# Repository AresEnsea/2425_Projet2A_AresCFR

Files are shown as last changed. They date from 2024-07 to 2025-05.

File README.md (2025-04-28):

# 2425_AresCFR
Ce repository contient le travail de l'association Arès dans le cadre de la Coupe de France de Robotique 2024-2025. Il contient tous les fichiers CAO, Kicad, Python, C ainsi que les photos, diagrammes et schémas qui ont fait avancer le projet.

## Répartition
Dépôt du projet de coupe de France de robotique 2024/2025
- 1A : Ce repository contient le travail des 1ères années membres de l'association Arès à l'ENSEA sur les PAMIs de la Coupe de France de Robotique

Read me 1A :
      https://github.com/AresEnsea/2425_Projet2A_AresCFR/blob/main/1A/README.md
      
- 2A : Ce repository contient le travail des 2èmes années membres de l'association Arès à l'ENSEA sur le robot principal de la Coupe de France de Robotique

Read me 2A :
      https://github.com/AresEnsea/2425_Projet2A_AresCFR/blob/main/2A/README.md

WhatsApp Image 2025-04-28 at 09 13 59
WhatsApp Image 2025-04-28 at 09 14 00

https://github.com/user-attachments/assets/8da76ca9-4337-4687-90c1-276035e22721

PAMI_img1

## Règlement
Le but de la compétition est de faire réaliser des actions de différentes difficultés grâce à des robots complétement autonomes, en lien avec le thème de l'année. Cette année le robot principal devra pouvoir se déplacer, déplacer des cannettes et des planches en bois de sorte à les empiler selon l'ordre suivant (2 canettes - 1 planche, 2 canettes - 1 planche , 2 canettes - 1 planche) pour un maximum de 3 étages, chaque étage rapporte plus de points que le précédent, le tout pour atteindre le score le plus grand. Cette année les PAMIs (Petits Actionneur Motorisés Indépendants) censés aider le robot principal en rapportant également des points sont d'une grande importance puisque rapporte en théorie autant de points qiue le robot principal, ils réaliseront des actions simples (déplacement et activation d'un actionneurs), un se distingue parmi eux le "Superstar" qui devra grimper sur l'estrade de la table et se rapprocher le plus du bord sans tomber pour gagner des points.




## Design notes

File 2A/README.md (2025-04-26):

# CDF-2025
Github de la Coupe de France de Robotique!

#REGLEMENTS
https://www.coupederobotique.fr/accueil/le-concours/reglement-2025/
https://www.coupederobotique.fr/wp-content/uploads/Eurobot2025_Rules.pdf

#DIAPO 
[https://enseafr-my.sharepoint.com/:p:/g/personal/antoine_lemarignier_ensea_fr/Eb2eWKZeK-NNrEKdino8REcB281sSVFofJ1WQgk0IBzqbg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](https://enseafr-my.sharepoint.com/:p:/g/personal/antoine_lemarignier_ensea_fr/ESafam9fs7ZCg727WFCmVboB-b12O3MPg7kT_spCKCZYLA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)

## Photo Robot :


## Liste des participants :
- Lorenzo ROMEO
- Antoine LEMARIGNER
- Mateo GOMES
- Nathan BAINARD
- Ewan ZAHRA-THENAULT
- Khalid ZOUHAIR
- Abderhamane EL FELSOUFI 
- Mohamed EL KOURMISS 
- Sammy GROS
- Matis GARBEZ
- Kenny SAINT FLEUR

## Partenaires :
- [x] Wurth
- [x] Elsys Design
- [x] RS
- [x] Acksys

# Etat du Projet 

## PCB MOTHERBOARD : 
- lien : https://github.com/AresEnsea/2425_Projet2A_AresCFR/edit/main/2A/Hardware/Hardware_%C3%A9lectronique/MainBoard/PCB_test/
- [x] Actuellement en V2
## PCBs auxiliaires :
- [x] steppers https://github.com/AresEnsea/2425_Projet2A_AresCFR/tree/main/2A/Hardware/Hardware_%C3%A9lectronique/Auxiliairy_board/PCB_Stepper
- [x] Moteurs base roulante https://github.com/AresEnsea/2425_Projet2A_AresCFR/new/main/2A/Hardware/Hardware_%C3%A9lectronique/Auxiliairy_board/PCB_Moteur
- [x] Servo moteurs https://github.com/AresEnsea/2425_Projet2A_AresCFR/tree/main/2A/Hardware/Hardware_%C3%A9lectronique/Auxiliairy_board/PCB_Servo

## Méca :
lien modèle 3D : https://cad.onshape.com/documents/e7dd6126290aaac8861c9b96/w/d5c385b6723083ea50ea9e11/e/9022f36f38f961f67dfb7efc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
- [x] Base roulante du robot complète
- [x] Pinces attrape canettes
- [x] Chariots élévateurs
- [x] Banderole
- [x] Fixations PCB
- [ ] Management de cables
- [ ] Odométrie
- [ ] Bouton d'arret d'urgence
- [ ] Tirette de démarrage

## ROS2 embarqué
- lien workspace ros : https://github.com/AresEnsea/2425_Projet2A_AresCFR/tree/main/2A/Firmware/ros2_ws
- [x] Liaison UART pi-STM32
- [x] Rosbags moteurs-actionneurs-Lidar
- [x] Interface écran
- [ ] Odométrie
- lien workspace lidar : https://github.com/AresEnsea/2425_Projet2A_AresCFR/tree/main/2A/Firmware/ydlidar_ros2_ws
- [x] Scan fonctionnel
- [ ] Tout mettre dans le workspace principal

## STM32
lien projet STM32 : https://github.com/AresEnsea/2425_Projet2A_AresCFR/tree/main/2A/Firmware/STM32_moteurs
- [x] V1 code stm32 moteurs réagissant à la pi
- [ ] V2 sur le microprocesseur du PCB

## Vision
lien projet Vision : https://github.com/AresEnsea/2425_Projet2A_AresCFR/tree/main/2A/Vision
- [x] Calibration caméra
- [x] Détection Aruco de la table
- [x] Suivi du mouvement d'un Aruco
- [ ] Transformer les informations de la caméra en carte pour le ROS

## Réseau
- [x] Administration de routeurs
- [x] Ping à travers 2 routeurs
- [x] Avoir un réseau transportable à la Coupe
- [ ] Connecter la pi et la jetson à un même réseau wifi pour communiquer
   
# Répartition par tâche :

## 1-ROS2/STM32 :
- Antoine
- Mateo
- Sammy

Le compte rendu de notre équipe sur le software embarqué se trouve dans le ReadMe.md du dossier Firmware :
https://github.com/AresEnsea/2425_Projet2A_AresCFR/blob/main/2A/Firmware/README.md

## 2-Traitement Image :
- Khalid
- Mohamed
- Abderahmane

Le compte rendu de notre équipe sur le traitement d'image est présent ici :
https://github.com/AresEnsea/2425_Projet2A_AresCFR/blob/main/2A/Vision/README.md

## 3-PCB :
- Kenny
- Ewan

Le compte rendu de notre équipe sur le PCB est présent ici :
https://github.com/AresEnsea/2425_Projet2A_AresCFR/tree/main/2A/Hardware/Hardware_électronique/readme.md

## 4-Mécanique :
- Lorenzo
- Matis
  
Le compte rendu pour la partie mécanique est disponible ici :
https://github.com/AresEnsea/2425_Projet2A_AresCFR/tree/main/2A/Hardware/Hardware_Mécanique/README.md

## 5-Réseau :
- Nathan
  
Le compte rendu pour la partie réseau est disponible ici :
https://github.com/AresEnsea/2425_Projet2A_AresCFR/tree/main/2A/Reseau/README.md

## 6-Planification :
- Mateo
- Antoine

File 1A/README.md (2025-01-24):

# Projet PAMI - Coupe de France des 1A

Ce projet consiste en la conception et la construction des robots **PAMI** pour la Coupe de France de Robotique.

## Description du robot actuel

Le robot actuel est équipé des éléments suivants :  
- Un **module suiveur de ligne** avec **4 capteurs/récepteurs infrarouges**.  
- Un **servomoteur** utilisé pour l'algorithme d'évitement d'obstacles.  
- Un **module ultrason** pour l'estimation des distances et la détection d'obstacles.  
- Une carte **Nucleo** pour la commande et la gestion des données.  
- Un **shield** (de dimensions 4,5 cm x 6,5 cm) permettant de connecter les composants entre eux.  
- Des piles rechargeables **Ni-MH 7,2V 2Ah** pour l'alimentation.  
- Deux **moteurs DC à engrenages métalliques** assurant la propulsion.  

### Images du robot actuel

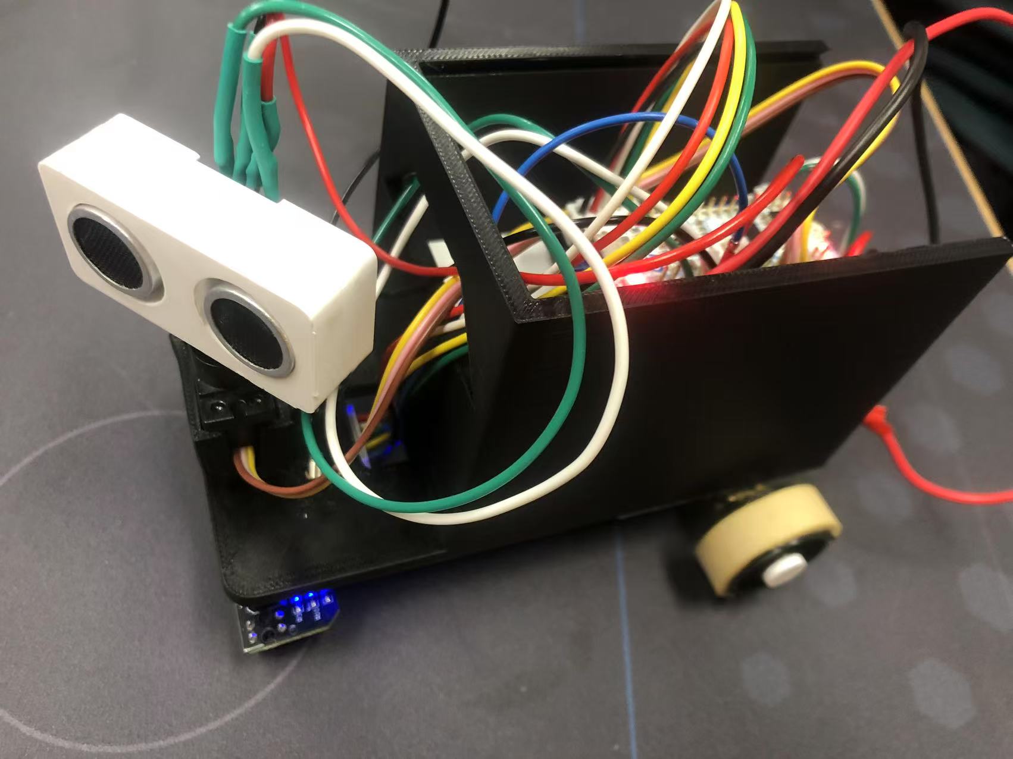
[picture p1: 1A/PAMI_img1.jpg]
Robot PAMI - Vue 1
  
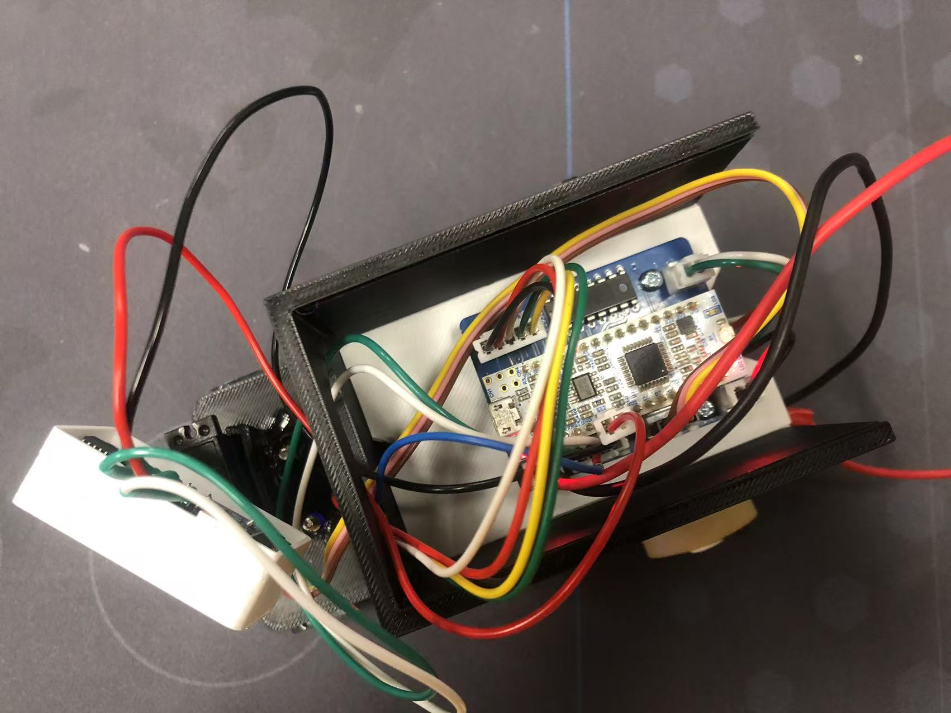
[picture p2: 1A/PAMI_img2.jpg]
Robot PAMI - Vue 2
  

---

## Nouvelle version en cours de développement

Nous avons commencé la conception de la prochaine version du robot **PAMI**, qui sera équipée des améliorations suivantes :  
- Un **PCB 4 couches** (de dimensions 4,5 cm x 5,5 cm), conçu pour intégrer directement le contrôle de tous les composants du robot.  
- Deux **servomoteurs** :
  - L’un dédié à l’algorithme d’évitement des obstacles.  
  - L’autre utilisé comme actionneur pour diverses fonctionnalités.  

### Images du PCB :

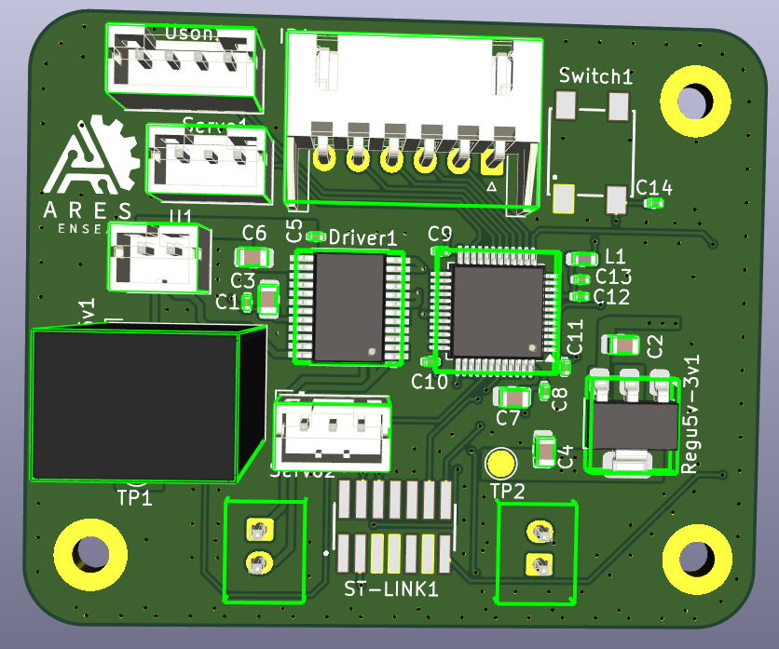
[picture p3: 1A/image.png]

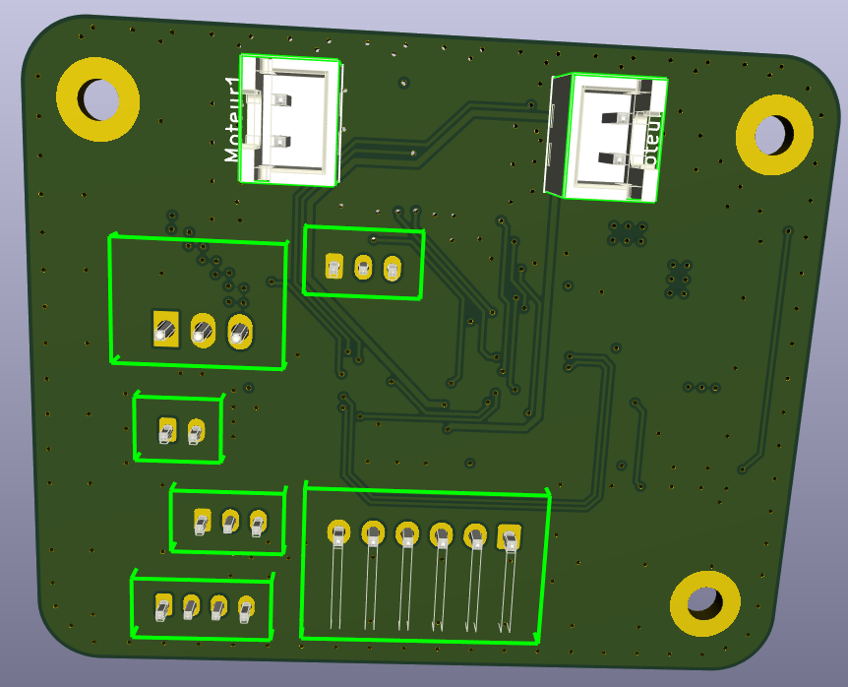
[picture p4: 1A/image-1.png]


---

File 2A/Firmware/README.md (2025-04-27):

Ici le dossier Firmware du Github de la Coupe de France 2025 d'Ares, il regroupe les fichiers C,C++ et Python qui seront utilisés pour programmer le robot principal.

# Algorigramme Robot 


Au démarrage du robot, regroupé sous l'action Init, plusieurs fonctions se lancent : poser la bannière, démarrage du package LiDAR. Ensuite l'action du robot reste simple : il suit le chemin indiqué par la jetson, exécute l'action de poser ou de prendre les canettes/planches et recommence. La fin de l'opération cannettes/planches sera vérifiée grâce à des switch. 

# Contenu

- ros2_ws : le workspace ROS actuellement sur la pi4 (booté avec Ubuntu 22.04 et utilisant ROS2) : lien https://github.com/AresEnsea/2425_Projet2A_AresCFR/tree/a82bbcb8feb8a41b16a1ad06d5899020270ff6f9/2A/Firmware/ros2_ws
  >- serial_node.py : on envoie une succession de chiffre (messages de 8 chiffres) en UART vers la STM
  >- serial_node_2.py : on envoie le message en fonction de l'input fait sur le clavier ce qui permet de controller par exemple la base roulante à distance
  >- serial_node_3.py : semblable à la node précédente mais on enrgistre en plus le message envoyé à la stm dans un rosbag pour pouvoir le rejouer ensuite (on créé notre propre topic "keyboard_commands")
  >- serial_node_4.py : on a une node "attentive" aux messages publiés sur le topic "keyboard_commands", qui attends les messages et les envoie dans l'UART.
  >- test_uart_lidar.py : on publie les distances (normalement) mesurées par le Lidar (reliés directement en UART à la pi), mais les valeurs varient beaucoup assez vite, donc à corriger ( faire des moyeenes ou un seuil de décision spécial).
  >- tirette_node.py : lié au topic "tirette_value" qui donne le départ pour lancer un bag dans la node robot_control et de lancer le robot.
  >- screen_reader : reçoit de l'uart entre l'écran et la pi le file que l'on souhaite lancer puis le publie sur le topic "file_stm_choisi"
  >- robot_control : (plusieurs) node(s) qui améliore les serial node 
  >- bagfile_stm32.py : node attentive au topic "file_stm_choisi", qui le lance en réaction (le bag permettant 
  >- launch_robot : node qui regroupe toutes les actions du robot ci dessus (lidar, écran, connexion série)
  >- ros2_startup.sh : script shell qui lance le launch au branchement de la pi (ne nécessite pas de wifi) 

- ydlidar_ros2_ws : le workspace du lidar qui nous sert de test pour l'instant mais qui sera rajouté dans notre workspace principal
   >- ydlidar_launch_view.py : avec un logiciel de visualisation 3D, nous voyons l'ensemble des points définis par le lidar.
   >- ydlidar_launch.py : renvoie les distances prises en considération par le lidar.
<image src="https://github.com/user-attachments/assets/174b4c74-a171-4f48-ac5a-31af73da478c" alt="image" width=300/>

-tirette : la tirette est associée à un gpio input et la pi en fait un topic binaire permettant de lancer un bag en début de partie <br/>


- code stm : [2A/Firmware/STM32_Final](https://github.com/AresEnsea/2425_Projet2A_AresCFR/tree/2238ea4a40f98718d38bb55b3ef729a7ff422c1b/2A/Firmware/STM32_Final)
  - cfr_mot2 : code pour la "carte mère", la carte redistribue le message reçue de la py dans les autres stm.

  - servo_ares_board : code qui permet de contrôler les servos moteurs.

  - stepper_ares : code qui récupère le message en uart et qui contrôle les stepper.
  
  - ecran_code_2425 : projet permettant d'afficher sur un écran lcd le plateau de jeu de la coupe de France. 
<image src="https://github.com/user-attachments/assets/786938ef-1c37-4f8c-b087-20cfafe1b13b" alt="image" width=300/>

## Protocole de communication :
Message de taille N, à augmenter selon les besoins 
Pour le moment le protocole est le suivant : " dir_mot_D | speed_mot_D | dir_mot_G | speed_mot_G  | servo | stepper"
Avec le nombres de bytes accordés à chaque variables : "1 | 4 | 1 | 4 | 12 | 4" 

https://github.com/user-attachments/assets/22d95b05-f980-4ab3-9817-96d0321312c0

Soit 26 caractères au total, à savoir que le premier bit de chaque moteur donne le sens les bytes derrière la valeur de vitesse (réinterprétée par la stm), les servo varient tous entre 0 et 1 et les stepper entre 0, 1 et 2 pour pouvoir les faire monter, descendre et laisser immobiles.

## Liste des topics 
-"keyboard_commands" envoyés par les nodes "serial_node_X" pour communiquer en UART avec la STM32, de la forme décrite ci-dessus. <br/>
-"scan" topic propre au lidar qui envoie les ranges (float) et l'intensité (float)  du laser pour chaque angle.<br/>
-"stop_moteur" le topic booléen que l'on tournera a 1 si le robot doit s'arrêter, il sera alors communiqué au reste des nodes du robots (moteurs, actionneurs).<br/>
-"bagfile_stm32" le topic dans lequel la node 
-"tirette_value" binaire qui permet ou non de lancer le bag en fonction de l'état de la tirette 
-"file_stm_choisi" en fonction du bouton cliqué sur la stm32 disco (écran)

# ROS Terms
- Rosbag : fichier qui enregistre des données des topics ROS pour les rejouer ensuite.
--> un rosbag peut par exemple enregistrer les données d'un topic "lidar" et d'un topic "wheels" pour rejouer les données (extension .deb3)
- Topic : message de types différents (int, bool, char, ...) qui s'échangent entre les nodes (node pubisher et node subscriber)
--> pour un Lidar, les données peuvent être envoyées avec un topic "lidar_data" avec un en-tête qui donne les paramètres puis les données de tout type (voir le package lidar-driver).
- Node : processus (fichier en python ou en C++ ici) qui effectue une action, un projet comprend généralement de nombreux nœuds.
--> dans notre projet par exemple les fichiers "serial_node_X.py" envoie de manière différente des données via uart à la pi

# ROS workspace objectif


# Fait 
- Communication Pi-STM32 : notre code en C avec les nodes ROS nous permettent de controler plusieurs PWM grâce à un message en UART envoyés à intervalles réguliers (ainsi que les GPIOs).
- Rosbag : nous pouvons enrgistrer aisément des bags avec les messages envoyés à l'UART même si nous semblons rencontrer certaines difficultés à les rejouer avec le bon timing, nous y travaillons.
- Lidar : une node ROS nous permet de lire les données du Lidar.
- Ecran : l'écran nous permet de selectionner un bag.
- Commande pinces : on peut aisément controler les servo et les stepper depuis la pi.
- Tirette : la tirette permet de donner le départ.

# A venir :
- Odométrie : dès que nous aurons un PCB opérationel nous nous empresserons de commencer l'odométrie

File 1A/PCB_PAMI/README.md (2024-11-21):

# Hello ici c'est le PCB

## déposer votre projet KiCad

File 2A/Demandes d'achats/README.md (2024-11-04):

|Composant|Prix|Qté|Total|Lien|
|:----:|:---:|:---:|:---:|:----|
|Billes 12.7mm|11.90€|6|71.4€|https://fr.rs-online.com/web/p/billes-porteuses/2006385|
|BMS 24V 30A|15.53€|4|62.12€|https://www.amazon.fr/DALY-Batterie-protection-d%C3%A9quilibrage-batterie/dp/B09151BX18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|
|Electroaimants|7.99€|1|7.99€|https://www.amazon.fr/Namvo-Lot-aimants-KK-P20-%C3%A9lectromagn%C3%A9tiques/dp/B08NYFX8BV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|

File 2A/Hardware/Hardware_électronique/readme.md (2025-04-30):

# Rapport de fin de semestre :

Durant ce semestre notre équipe à pu réaliser différents PCB...

## PCB_ MotherBoard



### Description : 
 - La carte mère permet l'alimentation et la laison des péripériques (capteurs, actionneurs...) 
au microcontrolleur (STM32H735) les commandants et permet également à la stm32 de communiquer
avec un raspberry pi qui ferait du traitement d'information ainsi que la communication vers l'extérieur 
via le WIFI.

### Features Principales: 
 - 9 liasons inter cartes : connecteur JST4 (1 UART + alimentation 24V).
 - Shield pour Raspberry Pi assurant l'alimentation 5V ainsi qu'une liason UART.

### Issues :
 - Malheuresement, suite à une erreur d'empreinte, le PCBMotherBoard 

## PCB_Moteur V3


### Descriptopn :
 - Carte de pilotage des moteurs de la base roulante. Nous avons prévu une carte par moteur.

### Caractéristiques techniques : 
- Supporter les appels de courants jusqu'à 10A par moteur.
- Connction des sondes à effet hall du moteur en RS323.
- Connection du moteur en XT30.
- STM32G474 embarquée pour communiquer avec la carte mère ainsi que les différents péripériques de la carte.
- Capteur de Température.
- Sondes à effet Hall pour la mesure de courant instantané consommé par le moteur.
- Possibilté de brancher un ventilateur.
  
### Issues :

-  La V1 du PCB n'a pas été concluante suite au non fonctionnement d'un convertisseur buck. Celui-ci à été changé dans la V2.
-  La V2 à fonctionné mais avec un problème qui faisairt que le moteur ne touranit que dans un sens. La V3 rajoute une resistance de sense entre le bras de pont et le mosfet driver. 

## PCB_Stepper 

### Description :
 - Carte de pilotage pour 2 steppers steppers.

### Caractéristiques principales : 
 - Supporte l'eau la plie les pets et le vent grâce aux 2 TMC2225 embarqué pour le pilotage des steppers.
 - STM32G071 embarquée pour la liason UART avec la carte mère ainsi que la commande des moteurs...

### Issues :

- V1 actuelle .
- Pour la V2 ce serait bien de mesure de courant en instantané.

# PCB_Servo


## Description :
- Carte servant d'intermédiaire entre la mainboard et tous les servos du robot

## Caractéristiques techniques :
- Le connecteur JST 4 pins recoit la puissance et une information UART de la carte mainboard.
- La puissance est convertie de 25.2V en 7.4V pour alimenter les servos.
- Le 7.4V est convertie en 3.3V pour alimenter le microprocesseur STM32G071CBUx.
- L'information UART est traduite par le microprocesseur en un signal PWM par servo.

## Finalité:
Quatre PCB servos furent soudés. 
Trois sont opérationnels, cela nous permet d'en avoir deux dans le robot et un en réserve par sécurité.
En effet, un PCB servo peut commander 8 servos et il y a 12 servos à commander à la fois sur le robot.
Le troisième constitue une sécurité au cas ou une des deux cartes utilisées viendrait à casser (court-circuit, surcharge, choque...).

# Issues
- Le modèle de servo moteur devant etre utilisé à changé après avoir finis le routage, il a fallu alors reprendre le routage de toute la puissance de la carte
- Sur les quatre PCB soudés, tous ne fonctionnent pas parfaitement:
   Je ne suis pas parvenu à téléverser un quelconque programme sur le microprocesseur de la première carte que j'ai soudé. Celle-ci est donc considéré comme HS.
   La deuxième carte est opérationnelle mais je lui ai relevé deux défaults. Premièrement, elle délivre du 8,2V aux servos au lieu de 7,6V. Deuxièmement, je n'ai réussis qu'à souder 6 connecteurs JST pour relier la carte aux servos.
   Les deux cartes soudées en dernières fonctionnent parfaitement (aucun problème de fonctionnement relevé).
  
# Schéma Final du Hardware
En suivant ce lien vous trouverez un schéma de tous les PCB ci-dessus avec câblage entre eux :

https://lucid.app/lucidspark/aabfef21-1fd2-40bf-9924-298b6e461ffa/view

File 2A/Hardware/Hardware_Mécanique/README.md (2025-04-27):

# Rapport de l'équipe mécanique



La mécanique à été réalisée par ROMEO Lorenzo, GARBEZ Matis, avec une petite participation de YOUSFI Bilal qui a voulu réaliser les fixations pour les moteurs stepper des poulies.
On peut voir sur la photo ci dessus la totalité du robot assemblé. On y trouve donc la base roulante sur lesquels sont montés les moteurs ainsi que l'odométrie et les PCBs. Les rails linéaires fixés aux tiges d'alluminium extrudé afin de supporter les mécanismes de pinces élévatrices s'élevant par un système de poulie actionné par moteurs stepper. Ces tiges supportent la plaque supérieure sur laquelle sont montés les moteurs stepper actionnant les poulies mais aussi le LiDAR pour l'évitement d'obstacles, le routeur et ses antennes pour communiquer avec la NVidia Jetson, le support de balise monté au dessus du LiDAR, le bouton d'arrêt d'urgence et le mécanisme d'activation par tirette actionné par dépression d'un switch en enlevant la tirette.

Par ailleurs vous pourrez remarquer que la plaque supérieure est bien plus petite que la plaque inférieure. Cela permet d'empiler 3 étages et donc de répondre entièrement aux contraintes imposées par la compétition, malgré le 3 ème étage étant plus haut que la hauteur maximale autorisée du robot.

Tous les fichiers 3D sont disponibles sur OnShape via ce lien : https://cad.onshape.com/documents/e7dd6126290aaac8861c9b96/w/d5c385b6723083ea50ea9e11/e/9022f36f38f961f67dfb7efc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

## Base roulante

  Nous avons opté pour des moteur à courant continu MAXON, assemblé avec un réducteur et un encodeur afin de pouvoir développer un rapport couple-vitesse optimal et asservir la vitesse de rotation moteur.
  De plus nous avons redesigné le système d'accroche des encodeurs de roue ainsi que le système de billes porteuses. Ces èlèments sont désormais posés sur de ressorts ce qui nous a permis d'opter pour des roues de type compliant BaneBots procurant une excellente adhérence au robot facilitant le suivi de trajectoire.


  
Voici donc ci dessus la base roulante finale de notre robot

Capture d’écran du 2025-01-24 22-35-08

Vous pouvez observer ci dessus le système de suspensions de l'odométrie ainsi que des billes porteuses.

La projection verticale de cette plaque inférieure combinée à celle des mécanismes de pinces doit définir un périmètre de moins de 1200mm lorsque les mécanismes sont au plus compact et moins de 1400mm lorsque les mécanismes sont déployés. Nous avons bien fait attention à respecter cela, si bien que nous atteignont presque les 1200mm de périmètre lorsque le robot est entièrement déployé.

## Déploiement de la bannière

  Dans la compétition nous devons déployer une bannière de 50cm de long pour 25 cm de large. Nous pouvons la déployer sur le terrain ou contre la table. Pour éviter des problèmes avec le robot principal et les pamis, nous avons décidé de la déployer sur le rebord de la table. 
  Les règles imposent une taille maximal pour le robot, c'est pourquoi nous devions trouvé un mécanisme afin de pouvoir la plier en début de match et la déplier sur le rebord de la table. Dans un premier temps nous avions proposé un système totalement mécanique. Cependant, le déploiement n'était pas parfait et nous avions peur de ne pas répondre au critère de la compétition. C'est pourquoi nous avons optés pour un déploiement de la partie du haut de la banderolle mécanique et électronique avec un servo-moteur. 
  Ainsi la bannière sera déployée depuis un porte bannière, posé sur la pince du haut et poussé par les "bras" des pinces. On aura donc dans un premier temps la partie du bas de la bannière qui se déroulera par l'action de la pesanteur et du poids du mécanisme autour duquel la bannière est pliée puis enroulée. Ce dernier dépliera la bannière en fin de course grâce à la tension de ressorts comprimés par l'enroulement de la bannière.
  Nous avons opté pour ce système de déploiement car il reste relativement simple et efficace, il était nécessaire de plier ou d'enrouler la bannière car la réglementation impose une largeur et une longueur de bannière trop grandes pour etre stockées dans le robot comme tel.
  La partie du haut se déploiera par le même mécanisme mais uniquement quand le robot enverra la commande au servo moteur. Ainsi la bannière sera proprement déployeée. Le robot n'aura plus qu'à se déconnecté en roulant de l'autre côté de la bannière, ce qui déconnectera les pins header relié à la carte stm. 



Vous pouvez voir ci dessus la partie qui sera accrochée sur le bord de l'aire de jeu. La bannière y sera attachée entre les deux différentes plaques maintenues par un système de vis écrou. Les rebords extrudés de la partie grise ainsi que du bas de l'accroche de la partie bleue serviront à mieux maintenir la bannière enroulée lors de l'accroche du porte bannière sur le rebord de la table, et autoriser ensuite la chute du mécanisme de déploiement. On peut également y voir le trou pour le servo moteur et celui où les fils sortiront. 

https://github.com/user-attachments/assets/2ac68d6e-2b8b-40fc-8861-738e08470789

Capturevidodu24-01-2025230203-ezgif com-video-to-gif-converter

Ceci est une animation du système de déploiement de la bannière, il faut imaginer que tout comme pour le porte bannière, l'on attache la bannière en la serrant entre les plaques avec un système de vis écrous. Deux ressorts planaires de 180 degrés sont placées au sein des pivots afin d'exercer une force cherchant à déployer le mécanisme. Le mécanisme du bas est maintenu fermé en l'enroulant dans la bannière tendu que celui du haut est bloqué avec le servo-moteur.

## Pinces élévatrices



  Les mécanismes sont concus de sorte à transporter tout un étage de l'estrade comme tel et le déposer déjà monté. Il se base sur un mécansime à fils afin de resserer les pinces autour des deux "piliers" centraux de l'estrade et des bras viennent porter la planche supérieure de l'estrade. Ce mécanisme est monté sur un système de poulie et rail linéaire. Nous prévoyons deux mécanismes pour chacun des deux cotés du robot, soit la capacité à déplacer 4 estrades à la fois et aisni aisément construire deux estrades de deux etages.
De plus, à cela s'ajoute la possibilité de pouvoir porter deux etages déja assemblés avec une unique pince nous permettant donc de pouvoir empiler trois étages. Cela traduit donc une mécanique complète. Nous considérons qu'il ný a plus rien à améliorer d'un point de vue mécanique sur les pinces.
Le choix d'un mécanisme acctionné par des fils repose sur le fait de vouloir minimiser l'empreinte de la pince mais aussi le nombre d'actionneurs et donc de cablage et de STM32 à devoir gérer. De plus cela permet de développer tout de même une force importante et amplement suffisante pour porter meme plusieurs étages d'un seul coup.

Capturevidodu24-01-2025234327-ezgif com-video-to-gif-converter

Voici donc le fonctionnement des pinces principales actionnées par l'enrouleur central en gris et légérement déporté vers la droite actionné par un servomoteur KST, essentiel pour délivrer le couple nécessaire.

Capturevidodu24-01-2025234354-ezgif com-video-to-gif-converter

L'enrouleur central a été déporté afin d'autoriser le fonctionnement du mécanisme auxiliaire permettant de mieux englober la boite de conserve à soulever, assurant une prise à toute épreuve.

Capturevidodu24-01-2025234951-ezgif com-video-to-gif-converter

Ce mécanisme est responsable de soulever les planches posées sur les boites de conserve. Un switch est intégré dans les bras porteurs afin de reconnaitre facilement lorsque le chariot est placé de sorte à pouvoir soulever la planche avec certitude; cela est une redondance à l'exécution de la maneuvre de récupération d'un étage étant donné que l'élévation par steppers permet déjà une connaissance assez précise de la position verticale du mécanisme:

1. Le robot s'aligne à l'étage présent sur la table.
2. Il fait monter le chariot élévateur jusqu'à ce que les bras atteignent les planches
3. Il reserre alors les pinces afin d'attraper les canettes et soulève la totalité de l'étage.

## Support PCB :

Support pour PCB moteur, servo-moteur et stepper :
WhatsApp Image 2025-04-27 à 22 23 22_0c7d7915

Dans le cas où nous utilisons les PCBs conçus, nous avons proposé une tour à PCB qui controlent tout les moteurs du robot. Cette tour a été pensé pour qu'elle puisse réunir un maximum de PCB de la manière la plus ergonomique possible. Les PCBs s'y fixent par encastration et le support est encastré dans le bois de la base roulante. Ils sont placés stratégiquements à cotés des moteurs de chaque côté du robot. Ces pcbs sont alimentés par le pcb multiprise :

WhatsApp Image 2025-04-28 à 00 16 25_3da53bbe

Ce PCB est relié à un support qui reprend sa forme et qui installé dans le robot sur un rail afin de pouvoir ajuster sa position en cas de besoin. 

## Support antenne :

Le plus simple avec la place qu'il nous reste est de placé le routeur et les antennes au dessus du robot :



Elles sont proche du routeur fixé par ses mounting holes sur la plaque du haut. Un angle de 90° est mis entre les antennes comme demandé par l'équipe réseau. 

## Cable Management :

WhatsApp Image 2025-04-27 à 22 39 31_3f12c18c

Le cable management est encore en cours car dépend de l'utilisation ou non de PCbs. Cependant nous faisont ça le plus proprement possible avec de la gaine tréssée et de la gaine thermo.

##Tour Caméra :



Pour la vison nous avons réalisé une tour en 3 parties :
- La base:



Cette base est fixé à la table de jeux par vis (un écrou est incrusté dans le print) :



- La jonction :



Cette Jonction possède un embout mal pour s'encastrer dans la base et un embout femelle pour accueillir la tête avec la caméra.

- Tête :



La tête possède un trou pour fixer les caméras de l'équipe vision. 
Globalement cette tour est pratique car tout a été réfléchis pour qu'elle s'imprime sans support. Des lignes sur les côtés indiquent comment relier les parties de la tour. Il est ainsi plus aisé de la désassembler pour son transport. Les tolérences ont été calculées de manière à ce que les pièces soient facile à s'assembler et pratique pour orienter les caméras. 

## Conclusion

Dans l'ensemble nous avons répondu aux demandes de chacune des équipes tout en respectant les règles de la compétition. Le robot est assemblé !

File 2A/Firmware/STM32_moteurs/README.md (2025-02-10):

 -Ces directory s'utilisent avec les projets ROS associés qui gère l'UART, le premier permet d'envoyer simplement un 0 ou un 1 le deuxième permet de choisir le nombre de caractères dans le message UART (par défaut 4), il suffit dans le code STM32 de modifier la taille de "rx_data", par défaut à 7 pour 4 caractères dans le messsage, augmenter rx_data avec le nombre de caractère envoyés (4-7,5-8,6-9, etc).

-cfr_V1 : version finale du contrôle des moteurs en fonction de ce qu'il reçoit de la raspberry pi.

## Troubleshouting : 
Si problème en reprenant un projet stm32, penser à regénérer un binary (.elf) en suivant les instructions suivantes : 


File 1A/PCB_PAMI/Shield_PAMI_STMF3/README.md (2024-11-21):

# PCB_Pami_2024
Projet PCB pour le PAMI Coupe de France de Robotique 2425 ----ENSEA ARES

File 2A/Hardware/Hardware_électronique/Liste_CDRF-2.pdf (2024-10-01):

## Liste de matériel CDRF sur robot

Weidle Rémi

6 mai 2024

Couleur | Signification
Aucun | Minimum vital
Rouge | Jamais utilisé mais potentiellement utile
Vert | Communément utilisé et sans doute utile
Jaune | Peu utilisé ou pas utilisé mais utile

## Déplacement et Stratégie

Nom | Matériel | Commentaire
Roue G Roue D Roue encodeuse G Roue encodeuse D Lidar IMU Caméra Bumpers | Stepper Stepper Ref Ref Ref Ref Ref Ref | 4A, 17V 4A, 17V (3v3) (qq mA) (3v3) (qq mA) (5v) (100mA) (5v ou 3v3) (300mA) ... Sur le coté permet de savoir quand on cogne un mur

## Actionneurs

Nom | Matériel | Commentaire
Moteurs Moteurs Moteurs Moteurs Moteurs Piston Electroaimant | Stepper Servos Mcc Dynamixel ESC Ref Ref | 2, 3 en plus max 3,4 max 1, 2 en plus Marche aussi pour XL320, conn type Dynamixel Propulser ou aspirer | Max 1,2 Max 1 ou 2 Max 1 ou 2

1

## Capteurs

Nom | Matériel | Commentaire
Couleur Résistance IR Poussoir Capteur inductif | Ref ref ref ref ref | Plot, plantes, cubes, balles Pour vis à tête cruciforme passage d’éléments x2 passage d’éléments x2 passage d’éléments

## Communication

Nom | Matériel | Commentaire
NRF24 Bluetooth WI-FI 333Mhz 38Khz | Ref Ref Ref Ref Ref | / / / / /

## Sécurité

Nom | Matériel | Commentaire
BAU Fusible | Spec pour dimensions A voir selon cas | Accessible à hauteur Raspy, Robot général...

## Autre

Nom | Matériel | Commentaire
STM32 Raspy Jetson | Ref Ref Ref | Pour gérer des péripheriques Pour le reste... Pour le reste...

2

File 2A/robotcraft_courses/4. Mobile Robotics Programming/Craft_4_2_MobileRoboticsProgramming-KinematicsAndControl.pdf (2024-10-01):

# CRAFT #4

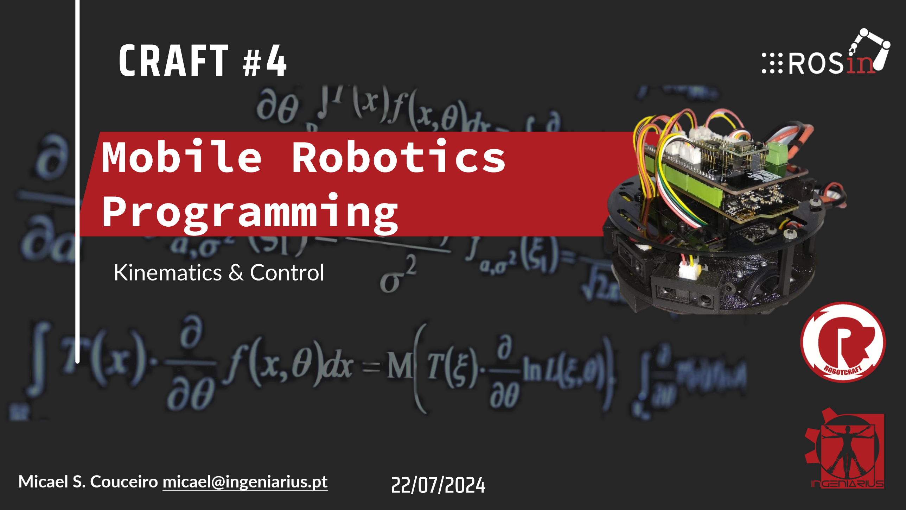
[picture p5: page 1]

22/07/2024

## Mobile Robotics Programming

Kinematics & Control

Micael S. Couceiro micael@ingeniarius.pt

# CONTENT

- Kinematics
- Initial concepts
oDifferential robots
- Control
- Initial concepts
oPID

# KINEMATICS

# KINEMATICS

## oFormal definition

“the branch of mechanics concerned with the motion of objects without reference to the forces which cause the motion.”

# KINEMATICS

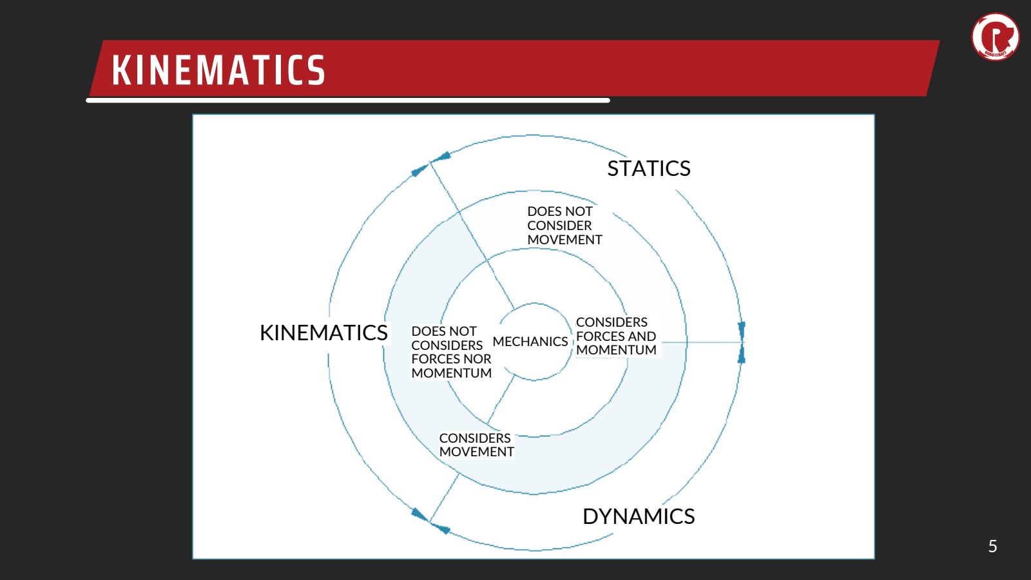
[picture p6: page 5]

KINEMATICS

DYNAMICS

STATICS

CONSIDERS
MOVEMENT

DOES NOT
CONSIDERS
FORCES NOR
MOMENTUM

MECHANICS

CONSIDERS
FORCES AND
MOMENTUM

DOES NOT
CONSIDER
MOVEMENT

# KINEMATICS

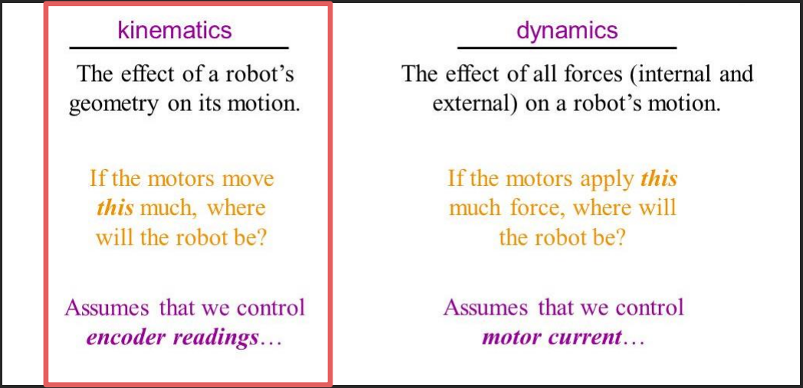
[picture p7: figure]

# KINEMATICS

- To localize a given rigid body in a 3D space, a reference coordinate system is associated to it (world reference or map reference)
- A reference associated to a rigid body is fixed on it – any point of the rigid body will have invariant coordinates in its own reference coordinate system
- The reference coordinate systems are defined by three orthogonal unitary vectors: (xො, yො, zƸ)

# KINEMATICS

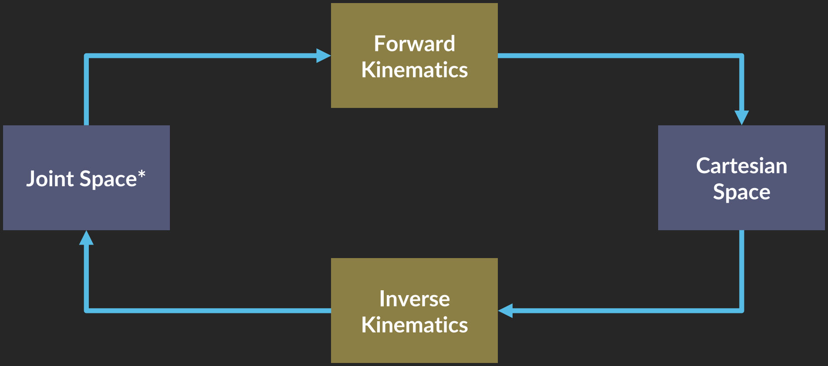
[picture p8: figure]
Joint Space*; Cartesian; Space; Inverse Kinematics; Forward Kinematics

*A typical differential robot can be considered as a joint itself

# KINEMATICS

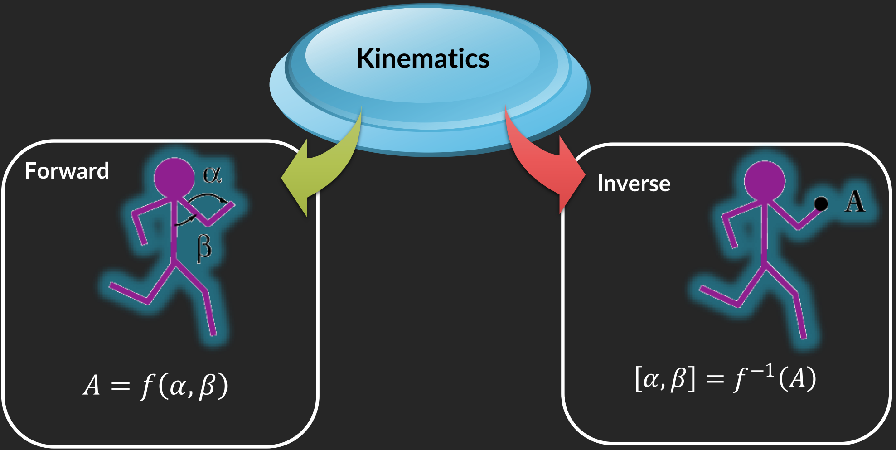
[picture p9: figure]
Forward; Inverse; Kinematics

# FORWARD KINEMATICS

- The forward kinematics allows to determine the Cartesian position of the links by knowing the angular orientation of the joints
- In the case of a mobile robot, it allows to determine its

Cartesian position considering the rotation of the wheels

# FORWARD KINEMATICS

- How would it be for 2 links (and 2 joints)?

# INVERSE KINEMATICS

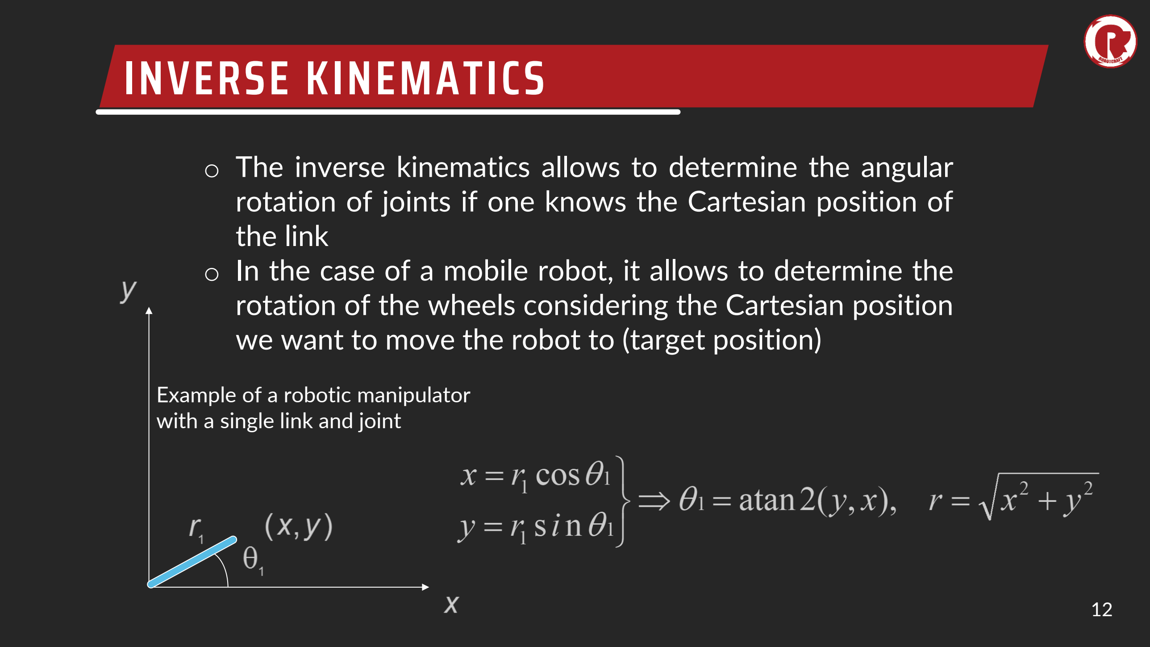
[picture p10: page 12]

- The inverse kinematics allows to determine the angular rotation of joints if one knows the Cartesian position of the link
- In the case of a mobile robot, it allows to determine the rotation of the wheels considering the Cartesian position we want to move the robot to (target position)

Example of a robotic manipulator with a single link and joint

# B UT H O W T O DE VELOP T HE KI NEMATIC MO DEL O F A MO BILE RO BOT?

This is where odometry kicks in…

# DIFFERENTIAL ROBOT

Workspace
Environment
World
Map
Inercial reference frame | /map TF

# DIFFERENTIAL ROBOT

ROBOT

moving reference frame

/base_link TF

# DIFFERENTIAL ROBOT

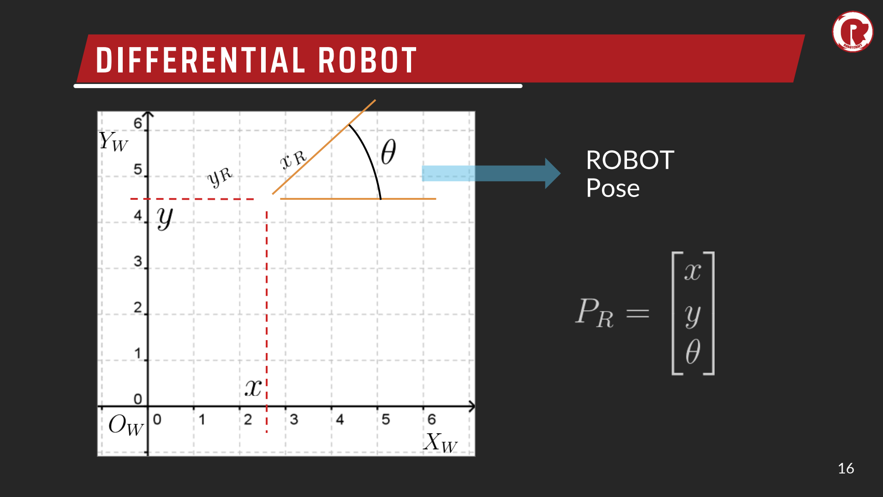
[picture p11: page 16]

ROBOT
Pose

# DIFFERENTIAL ROBOT

# DIFFERENTIAL ROBOT

# DIFFERENTIAL ROBOT

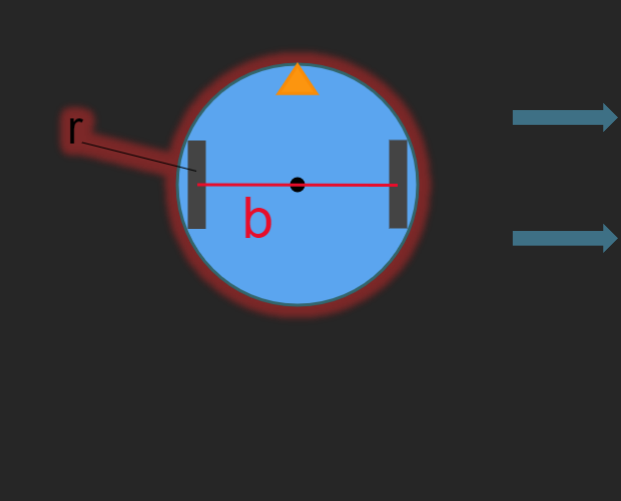
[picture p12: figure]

Radius of wheels

Wheel-to-wheel Distance

# DIFFERENTIAL ROBOT

Radius of wheels

Perimeter of wheels

Encoder Resolution
(Pulses per revolution)

Linear wheel displacement
For 1 pulse

# DIFFERENTIAL ROBOT

Odometry typically uses encoders to measure wheel rotation and/or steering orientation*

How can we know what is our position, given some particular movement?

Totally self-contained as it is always capable of providing the vehicle with an estimate of its position

The position error grows without bound unless an independent/external reference is used periodically to reduce the error

*Actually, that’s only one of the ways to obtain odometry – there are other ways to have an estimation of the odometry by employing other technologies (e.g., LIDARs) and methods (e.g., SLAM).

# DIFFERENTIAL ROBOT

## Displacement of the Wheels

Displacement of Left
Wheel

Displacement of Right
Wheel

Number of Pulses

# DIFFERENTIAL ROBOT

## Linear Displacement of the Robot

# DIFFERENTIAL ROBOT

Change in Orientation

# DIFFERENTIAL ROBOT

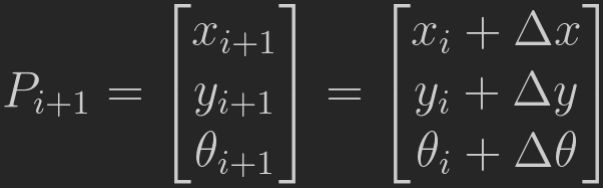
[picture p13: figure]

## Approximation!

# DIFFERENTIAL ROBOT

Algorithm Calculate Pose

:
1. Get the number of encoder pulses since last iteration
2. Calc linear distance
performed by each wheel
3. Calc linear distance
performed by the robot
4. Calc the change in
orientation
5. Update values in the
following order

# KINEMATICS – CHALLENGE #1

- Follow the sequence previously established and find out where the robot will be after 10 steps, considering that:
– The robot starts at the origin (0, 0), with r = 5 cm, b = 20 cm, C = 100
– The encoders provide the following readings at each iteration:
1. NLT = 0 & NRT = 0
2. NLT = 100 & NRT = 100
3. NLT = 300 & NRT = 200
4. NLT = 500 & NRT = 300
5. NLT = 700 & NRT = 400
6. NLT = 900 & NRT = 500
7. NLT = 1000 & NRT = 600
8. NLT = 1100 & NRT = 700
9. NLT = 1200 & NRT = 800
10.NLT = 1200 & NRT = 800

# KINEMATICS – CHALLENGE #1

- In Arduino, implement the algorithm to calculate the forward kinematics of the differential robot and evaluate it considering the given example. Verify your maths.
– encUpdate(t): Get the current number of encoder pulses (load each element of the given 10 × 2 matrix, at each iteration t) and return its difference

– poseUpdate(NL,NR,r,b,C): Returns new pose of the robot based on encoder pulses and the robot’s physical properties

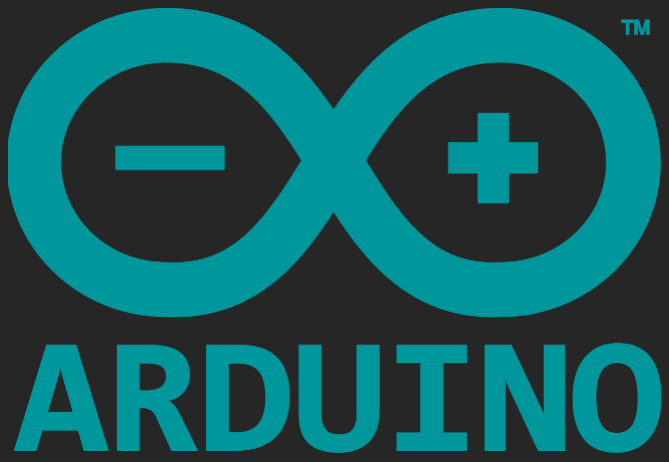
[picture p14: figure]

# IS THERE ANY USE FOR THE INVERSE KINEMATICS IN THIS CASE?

Yep. Move the robot from point A to point B is always useful (even though you can benefit from ROS’ navigation stack for that purpose)

# DIFFERENTIAL ROBOT

Inverse Kinematics: what wheels speeds do I need to perform the movements that I want?

With Odometry, we can now estimate, at every instant, our Position (x,y,θ).

Now, considering our current Position, what movements do I need to perform in order to go to a Goal Position?

# DIFFERENTIAL ROBOT

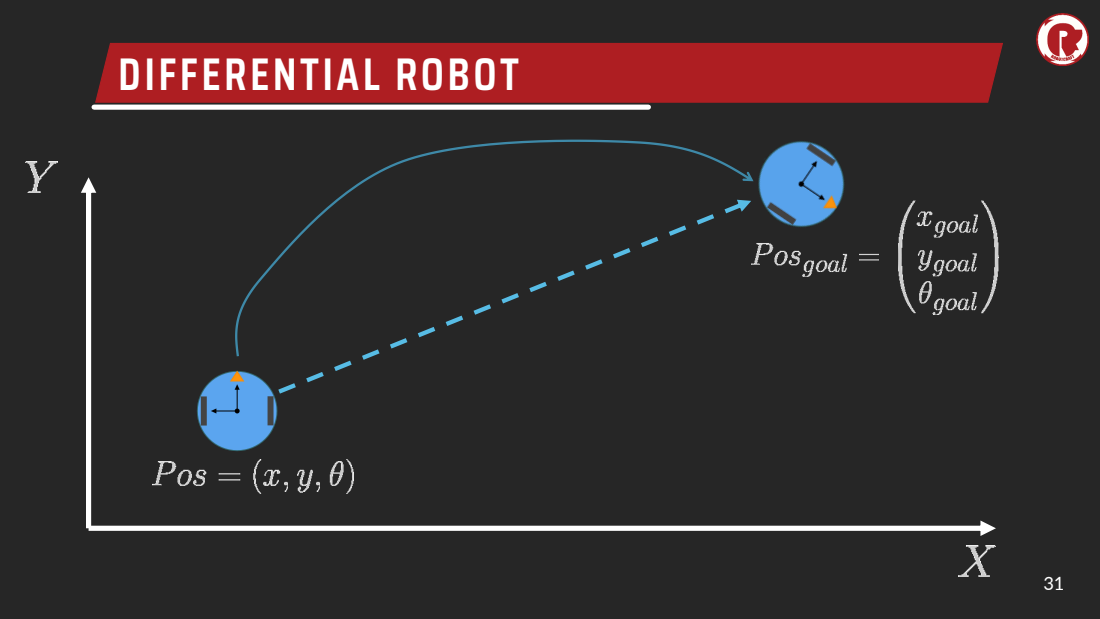
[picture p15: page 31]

# DIFFERENTIAL ROBOT

# DIFFERENTIAL ROBOT

# DIFFERENTIAL ROBOT

# DIFFERENTIAL ROBOT

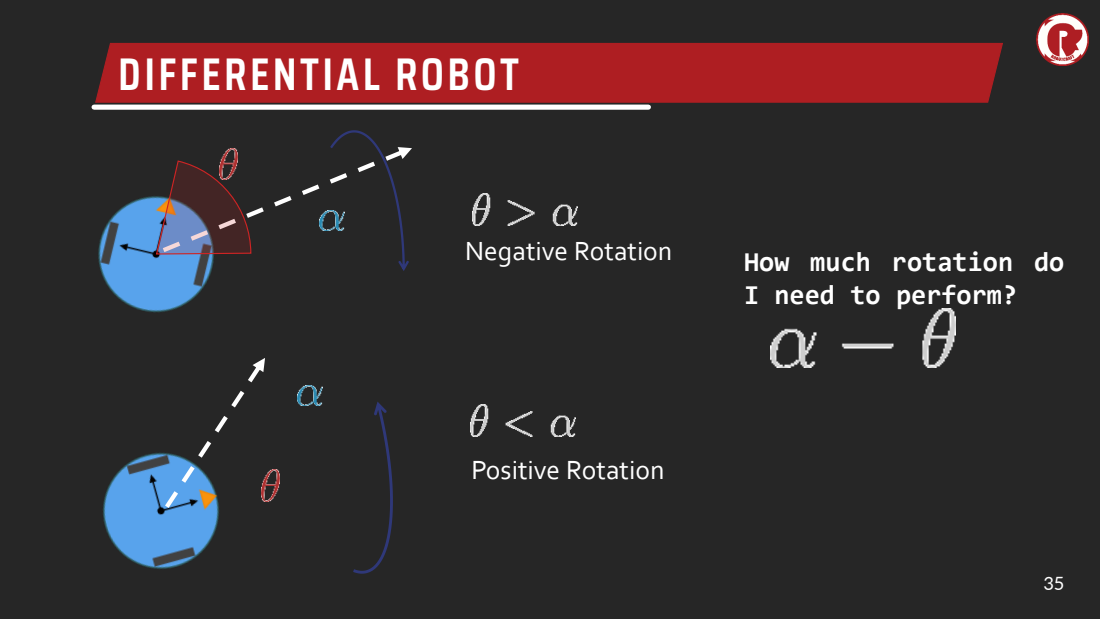
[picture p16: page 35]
Negative Rotation; Positive Rotation

How much rotation do
I need to perform?

# DIFFERENTIAL ROBOT

We can control the linear velocity v and the angular velocity w of the robot.

# DIFFERENTIAL ROBOT

Don’t forget about the sign!

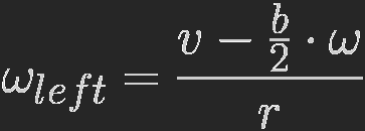
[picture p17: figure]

# DIFFERENTIAL ROBOT

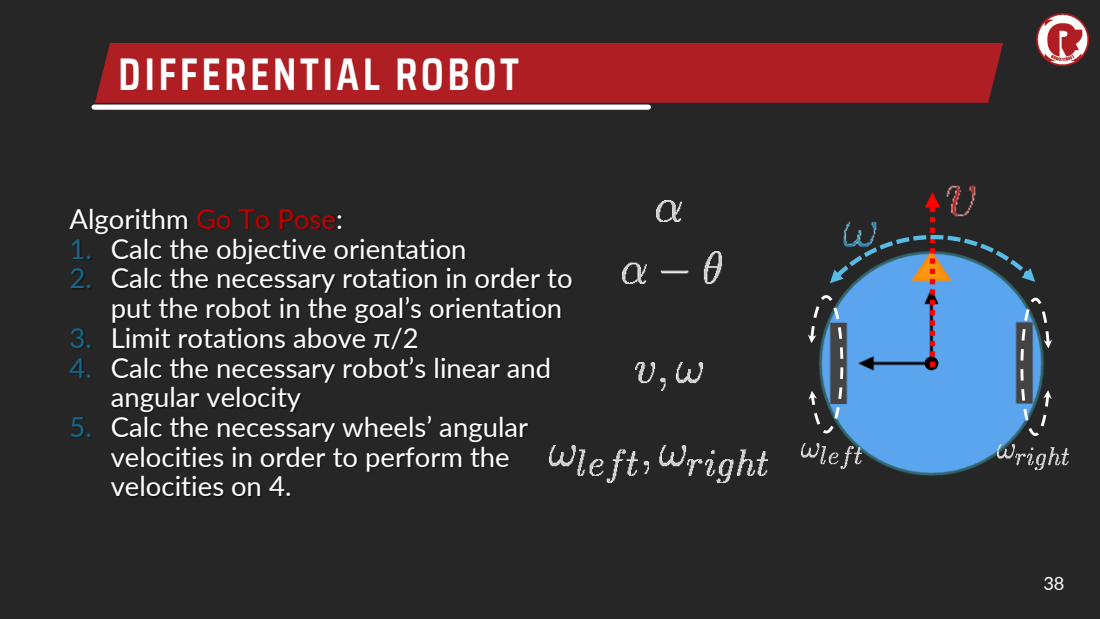
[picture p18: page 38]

Algorithm Go To Pose
1. Calc the objective orientation
2. Calc the necessary rotation in order to
put the robot in the goal’s orientation
3. Limit rotations above
4. Calc the necessary robot’s linear and
angular velocity
5. Calc the necessary wheels’ angular
velocities in order to perform the
velocities on 4.

# DIFFERENTIAL ROBOT

1. Get the number of encoder pulses since last
2. Calc real linear velocity and angular velocity

vi+1 =
C

2

∆t

wi+1 =

2 π r
C

NR − NL
b

1
∆t
3. Calc change in position and orientation

θi+1 = arctan2(sin(θi + wi+1∆t), cos(θi + wi+1∆t))

xi+1 = xi + vi+1cos(θi+1)∆t

yi+1 = yi + vi+1sin(θi+1)∆t

# DIFFERENTIAL ROBOT

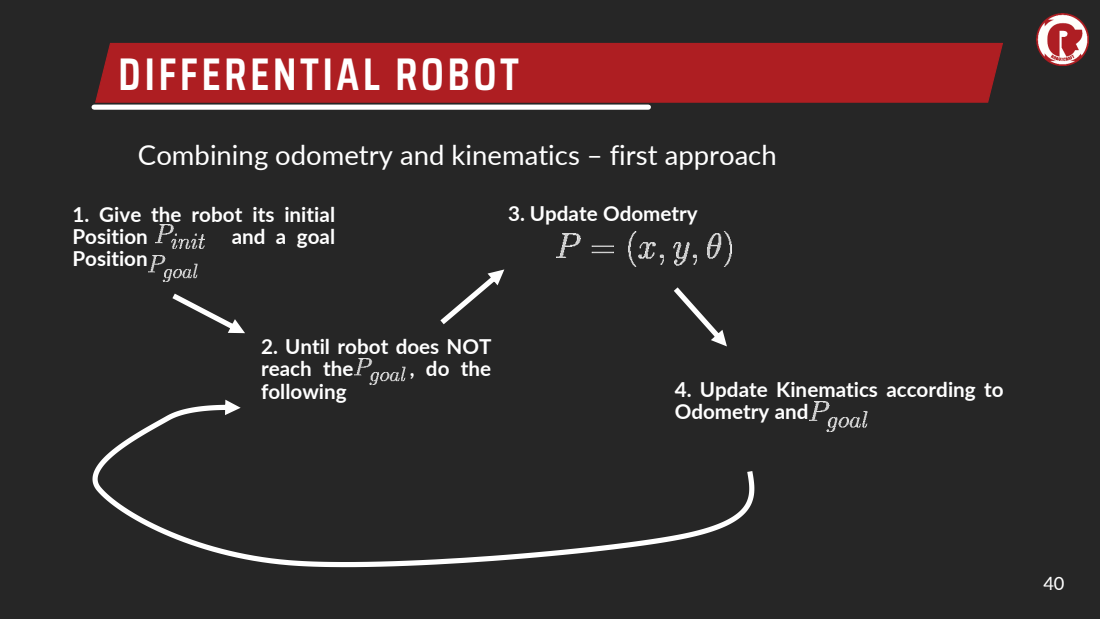
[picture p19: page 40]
Position; and a goal; reach the; , do the; 3. Update Odometry

Combining odometry and kinematics – first approach

1. Give the robot its initial
Position

2. Until robot does NOT
following

4. Update Kinematics according to
Odometry and

# DIFFERENTIAL ROBOT

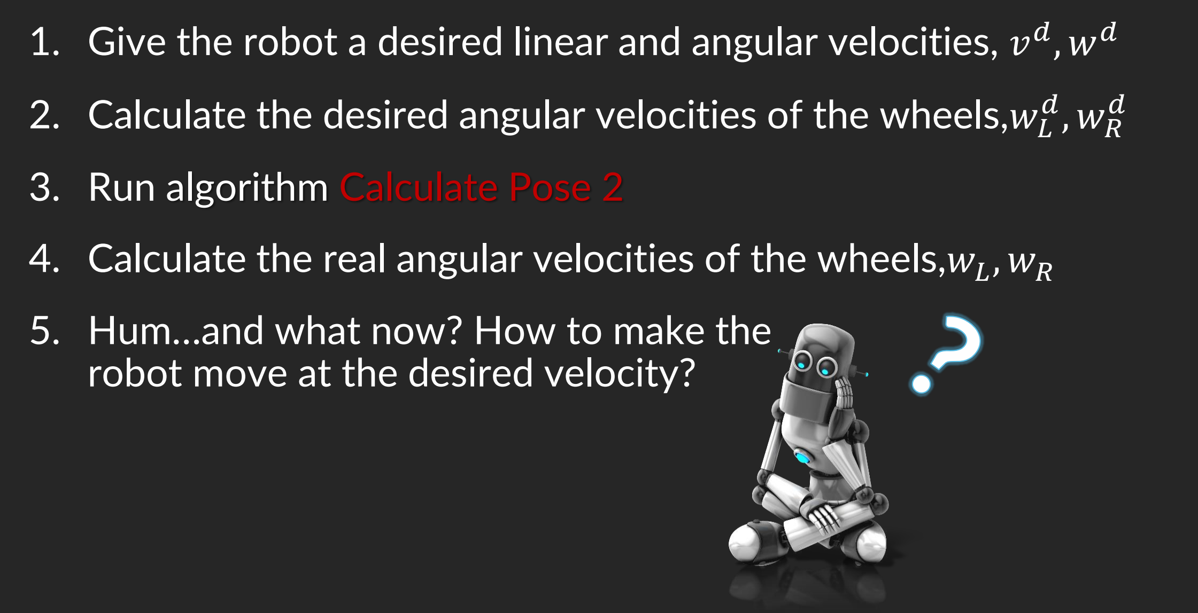
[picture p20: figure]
3. Run algorithm Calculate Pose 2; 5. Hum…and what now? How to make the robot move at the desired velocity?

1. Give the robot a desired linear and angular velocities, v
2. Calculate the desired angular velocities of the wheels,wL
4. Calculate the real angular velocities of the wheels,wL

Combining odometry and kinematics – second approach

# KINEMATICS – CHALLENGE #2

- In Arduino, adjust challenge #1 in order to calculate the forward kinematics of the robot and evaluate it considering the encoder data given before. Besides the existing functions, add those ones:
– cmd_vel(): Returns the desired linear and angular velocities (at this point, you can add constant values at will)
– cmd_vel2wheels(V, W): Converts the linear and angular velocities to wheels angular velocities
– poseUpdate(NL,NR,r,b,C): Besides returning the new position of the robot, also returns the real linear and angular velocities of the robot

# THAT’S WHERE CONTROL COMES!

By control, we mean the science of CONTROL THEORY.

# CONTROL

## - Formal definition

“interdisciplinary branch of engineering and computational mathematics that deals with the behavior of dynamical systems with inputs, and how their behavior is modified by feedback.”

# CONTROL

System – An interconnection of elements and devices for a desired purpose

Control System – An interconnection of components forming a system configuration that will provide a desired response.

Process – The device, plant, or system
under control. The input and output relationship represents the cause-and-effect relationship of the process.

# CONTROL

Open-Loop Control Systems
utilize a controller or control actuator to obtain the desired response.

Closed-Loop Control
Systems utilizes feedback to compare the actual output to the desired output response.

# CONTROL

Automobile steering control system

The driver uses the difference between the actual and the desired direction of travel to generate a controlled adjustment of the steering wheel

Typical direction-of-travel response

# CONTROL

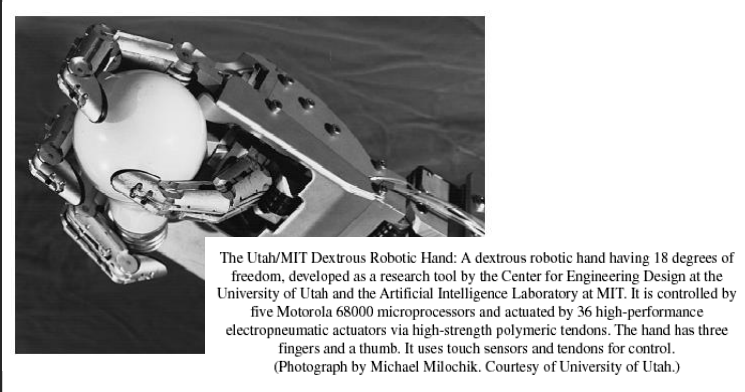
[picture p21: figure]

# CONTROL

# CONTROL

Boston Dynamics’ ATLAS robot can walk, run and jump in many different ways, including back and front flip.

# W H AT KI ND O F C O NTROL ME THOD C AN W E US E T O C ONTROL T H E S PE ED O F O U R RO BOT’S W H EELS?

The PID controller is one of the most widely used (alongside fuzzy logic) in the industry (e.g., robotic manipulators, AGVs, etc.) and mostly in our houses (e.g., AC, washing machine, etc.).
Let’s introduce the PID controller.

# PID

- More than half of the industrial controllers in use today utilize PID or modified PID control schemes (most of the time merged with fuzzy logic)
- When the mathematical model of the plant is not known and therefore analytical design methods cannot be used, PID controls prove to be quite useful

# PID

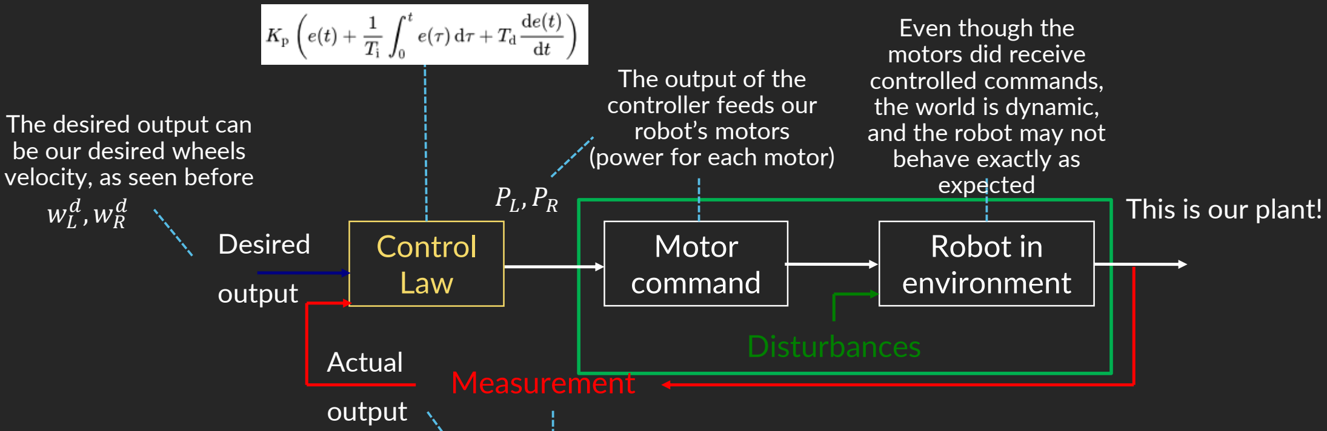
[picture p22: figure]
Motor command; Robot in environment; Control Law; Disturbances; Measurement; Desired; output; Actual; The output of the controller feeds our robot’s motors (power for each motor); Even though the motors did receive controlled commands, the world is dynamic, and the robot may not behave exactly as expected; This is our plant!; The desired output can be our desired wheels velocity, as seen before wL

In our case, the measurements (feedback) is provided by the motor encoders, which can be translated into wheel angular velocity (as previously seen) wL

, wR

# PID

- But what is the meaning of Kp

, Ki and Kd

?

- There are 3 components in the PID
– P = Proportional
– I = Integral
– D = Derivative
- Kp

, Ki and Kd

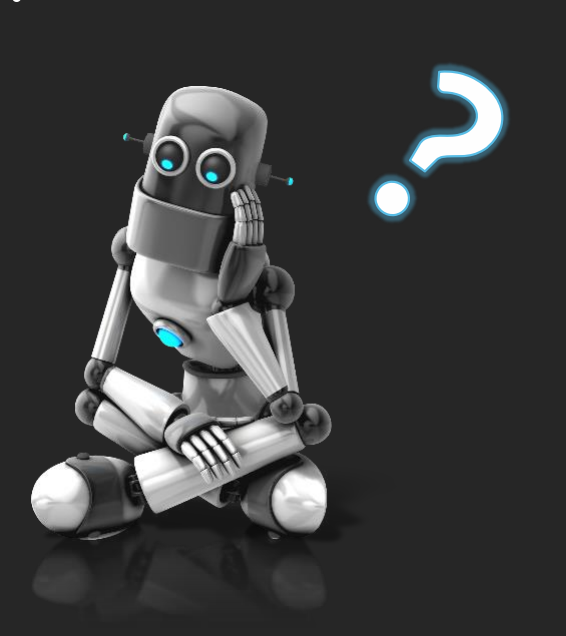
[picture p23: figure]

correspond to the gains of each component, respectivelly, necessary to reduce the proportional, integral and derivative errors.

# PID

- Play this game and share your thoughts regarding Kp

, Ki and Kd

:
https://sites.google.com/site/fpgaandco/pid-demo

Manipulate the gains of the controller

# PID

Response | Rise Time | Overshoot | Settling Time | SS Error
KP | Decrease | Increase | Small Change | Decrease
KI | Decrease | Increase | Increase | Eliminate
KD | Small Change | Decrease | Decrease | Small Change

# PID

But how to tune these gains to obtain the best response possible?

Many different types of tuning rules have been proposed in the literature.
- Manual tuning on-site (with support of Ziegler-Nichols rules)
- On-line automatic tuning (e.g., PSO)
- Gain scheduling (e.g., hybrid approaches or simple heuristics to adapt the gains based on specific responses/changes in the plant)

# PID

Ziegler-Nichols’ Rules for Tuning PID Controllers

- Ziegler and Nichols proposed rules for determining values of the proportional gain Kp

, integral time Ti

, and derivative time Td based on the transient response characteristics of a given plant.

- Such determination of the parameters of PID controllers or tuning of PID controllers can be made by engineers on-site by experiments on the plant.
- We need to apply a series of fine tunings until an acceptable result is obtained.

# PID

Ziegler-Nichols Method of Tuning Rule (one of them actually)
1. We first set Ti = ∞ and Td = 0, which implies using only the proportional control action.

Closed-loop system with a proportional controller.

# PID

2. We increase Kp

from 0 to a critical value Kcr, at which the output starts exhibiting sustained oscillations.

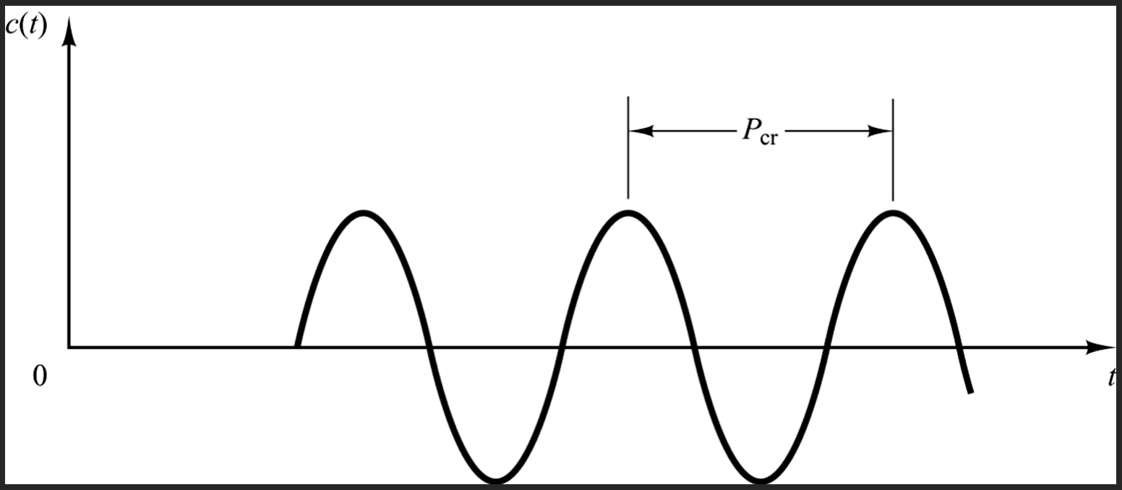
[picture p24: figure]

Sustained oscillation with critical period Pcr (Pcr is measured in seconds)

# PID

3. Ziegler and Nichols suggested that we set the values of the parameters according to these formulas:


Ziegler–Nichols Tuning Rule Based on Critical Gain Kcr and Critical Period Pcr

# PID

Disadvantages of Ziegler-Nichols method

- It can be time consuming if several trials are required and the process dynamics is slow
- Introducing oscillations into a process is, in many cases, not desirable (motors may suffer from current peaks)
- Will not work for an integrating process (streams comprised of gases, liquids, powders, slurries and melts do not naturally settle out at a steady-state operating level)
- Will not work for dead time dominant processes (dead time is the delay from when a controller output signal is issued, until when the measured process variable first begins to respond)
- Requires proper manipulation of the bias value by the controller or the person doing the tuning

Sometimes it is better to simply adopt a trial-and-error approach…

# PID

Limitations of PID control
- Tuning: largely empirical (e.g., Ziegler–Nichols method), unless one can easily acquire data and apply an optimization method (harder than it seems)
- Nonlinearities: can only be solved by integrating with other approaches, such as gain scheduling, multi-point controller, fuzzy logic
- Noise: use low-pass filter (may cancel out D → PI)
- Often PI or PD is sufficient…

# PID

1. Give the robot a desired linear and angular velocities, v
d

, wd
2. Calculate the desired angular velocities of the wheels,wL
d
, wR

d

4. Calculate the real angular velocities of the wheels,wL
, wR
5. Calculate the proportional error:

εPi+1

=

wL

d − wL
wR

d − wR

Application in the control of the differential robotic system:

# PID

6. Calculate the derivative error:

εDi+1

= εPi+1 − εPi

7. Calculate the integral error:

εIi+1

= εIi + εPi+1

# PID

8. Calculate the PID output and feed the motor driver with:

Gi+1 = KPεPi+1 + KIεIi+1

∆t + KD

εDi+1
∆t

# CONTROL – CHALLENGE #3

- In Arduino, implement a PID control for a DC motor equipped with an encoder (e.g. TinkerCAD: DC Motor with Encoder) with the following functions:
– encFunc(): Increments an integer variable (e.g., long int) each time it enters this function; the callback of the function should be triggered by an attachInterrupt (e.g., using pin 3) or by using the Encoder.h library
– pid_controller(): Runs the PID controller considering a given desired speed (it can be a constant value in an early phase and, afterwards, a potentiometer or a simple sequence of velocities) and the real speed calculated based on the difference between encoders’ pulses at the desired sampling rate
– TIPS:
- use function millis() to control the sampling rate at 100 ms
- set the desired speed between the whole range of possibilities, namely maximum speed
- use a single encoder phase and control in a single direction to start with

# CONTROL – CHALLENGE #3

# CONTROL – CHALLENGE #3


# CONTROL – CHALLENGE #3


Just a small code to test your dual-motor connections!

# CONTROL – Task

Adapt and merge the codes from challenge #2 and challenge #3 for the real hardware; i.e., for the motor driver, motor and encoder setup you will use in your robot. Control both speed and direction of both wheels considering a command velocity comprising linear and angular velocities,

following the previously presented scheme:; until the 28th July, 23h59; Motor command; Robot in environment; Control Law; Disturbances Measurement; Desired; output; Actual; The output of the controller feeds our robot’s motors (power for each motor); Even though the motors did received controlled commands, the world is dynamic and the robot may not behave exactly as expected; This is our plant!; In our case, the measurements (feedback) is provided by the motor encoders, which can be translated into wheel angular velocity (as previously seen)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

- This task should be completed

# CRAFT #4

22/07/2024

## Thank you

Micael S. Couceiro micael@ingeniarius.pt

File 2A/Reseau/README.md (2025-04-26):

# Rapport sur la partie réseau

Ce dossier réseau permet de conserver une copie des backups les plus récents pour les 2 routeurs utilisés pendant la coupe de France de robotique ( édition de 2025 )
# Objectif

Permettre à la partie vision de transmettre les informations recueillies des différents éléments de la table et de les transmettre au robot mobile ( voire aux pamis ) mais de façon isolée par un wifi local. Pour ce faire nous allons utiliser deux routeurs, l'un sur la base fixe avec la caméra et l'autre sur le robot principal.



# Matériel

## Routeurs de chez MikroTik



## WinBox 3.41
Le logiciel utilisé pour administrer les différents routeurs, voici son interface :


# Travail effectué

## Initialisation des routeurs

Mise en place d'un bridge entre l'interface wlan et ethernet de chaque routeur pour autoriser la communication entre ces deux interfaces. Mise en place des IP statiques de chaque routeur 192.168.88.10 pour le routeur de base ( routeur 1 ) et 192.168.88.20 pour le routeur "robot" ( routeur 2 ).

## Mise en place d'un wifi généré de façon locale

Le routeur 1 a été configuré pour émettre un wifi "wifi_from_base" et le routeur 2 a été paramétré pour s'y connecter. (si problème cf Table des problèmes plus bas)

## Configuration supplémentaire

Le wifi du routeur 1 utilise un serveur DHCP qui attribue des adresses à quiconque s'y connecte initialement prévu pour être dans la plage 192.168.88.100 - 192.168.88.199 j'ai restreint ce pool à 192.168.88.100 - 192.168.88.149 car il y avait des problèmes d'adressage d'ip, et que 50 ip devraient être largement suffisantes pour notre réseau local. Les ip devraient également s'attribuer dans le sens croissant.

Les tables de routages ont été configurées pour permettre la connection entre les connexions du routeur 2 aux connections du routeur 1

## Test de ping entre les routeurs
### Schéma de test : 


### On essaye avec le pc1 de ping le routeur 1 puis le routeur 2 : 


### On essaye avec le pc2 de ping le routeur 2 puis le routeur 1 : 


Les deux tests ont été réussis, les pings ont bien été envoyés et reçus ce qui prouve bien la connexion.

## Mise en place d'un DNS local

test d'attribution pour un ordinateur connecté en ethernet derrière le routeur 1


Depuis l'ordinateur connecté au réseau : 


 Attention : Avec l'ordinateur connecté en wifi il est possible de ping un pc connecté en ethernet au routeur, mais pour faire la manipulation inverse il était nécessaire de désactiver le pare feu windows (information à retenir pour la suite)

### Remarque :

Nous abandonnons la partie avec le switch physique nous permettant de se connecter à internet depuis le réseau local n'étant pas sûr d'avoir un câble RJ45 relié au réseau sur les lieux de la CFR, éventuellement nous pouvons faire des profils supplémentaires si le cas se présente

## Table des problèmes : 
### Impossible de se connecter au routeur ?
 -> assurez vous d'être sur le même réseau que le routeur : 
 
 -soit connectez vous à son wifi (s'il en émet un)
 
 -soit vous vous connectez à une box internet avec le routeur connecté en RJ45 dessus. Référez vous aux bonnes adresses mac présentes sur les routeurs si vous passez par une connexion filaire ou sans fil
### Problème de connexion entre le pc de commande et le reste :
 -> désactiver pare-feu 
### Problème de connexion entre les deux routeurs / Impossible de se connecter au wifi du routeur base avec PC :
 -> vérifier les bandes de fréquence du routeur base et du routeur robot pour qu'elles soient identiques
 
 -> pour la connexion avec le pc (du moins avec le mien) il faut utiliser le paramètre 20/40/80 Hz dans les bandes de fréquence du wifi avec comme paramètre de fréquence de 5GHz AC et non AX (qui correspondent respectivement au wifi 5 et au wifi 6)
### Moindre problème ?
 -> Ne pas hésiter à revenir sur une version précédente grâce aux backups localement enregistrés sur les routeurs (une version est aussi disponible pour le routeur base sur ce répertoir git), il faut aller dans la rubrique "file" à gauche dans winbox pour y accéder.
### Pour réinitialiser manuellement le routeur : 
 1. Couper son alimentation
 2. Maintenir le bouton reset
 3. Alimenter à nouveau le routeur en maintenant ce bouton enfoncé
 4. une fois que les LED commencent à clignoter, vous pouvez relâcher le bouton et attendre la réinitialisation du routeur
## Equipe réseau : 

### Respo réseau : Nathan

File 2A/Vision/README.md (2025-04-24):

# 🎯 Vision – Projet 2A ARES CFR (Coupe de France de Robotique)

Ce dépôt regroupe les travaux de l'équipe **Vision** pour le projet **2A ARES CFR**, dans le cadre de la **Coupe de France de Robotique**.

---

## 🧠 Objectifs du Système de Vision

Développer un système capable de :
1. **Détecter des éléments et marqueurs (ArUco)** dans un environnement robotique.
2. **Fournir une position précise** du robot en temps réel.
3. **Calculer des chemins optimaux**, en intégrant les contraintes dynamiques du terrain.

---

## 🔧 1. Calibration de la Caméra

### 🔍 Contexte
Calibration indispensable pour corriger les **distorsions optiques** et garantir la **précision** des mesures.

### 🧪 Méthodologie
- Utilisation d’un échiquier et de **ROS + OpenCV**.
- Détection des coins → calcul des matrices intrinsèques/extrinsèques.
- Validation avec modèle de reprojection.

### ✅ Résultats
- **50 images** utilisées, faible erreur RMS.
- Matrice intrinsèque + coefficients de distorsion.
- Tests validés sur maquette et en conditions réelles.

Calibration avec Chessboard
*Fig. 1 : Image utilisée pour la calibration.*

---

## 🧭 2. Détection des Marqueurs ArUco

### 📜 Contexte
Le règlement impose des marqueurs ArUco fixes sur le terrain. Ils servent de **points de référence** pour localiser le robot.

### ⚙️ Méthodologie
- Détection avec **OpenCV**.
- Extraction des IDs + calcul des vecteurs (translation & rotation).
- Tests en environnement réel, robustesse validée (lumière, perturbations).

ArUco sur table
*Fig. 2 : Marqueurs fixes définis par le règlement.*

### 🧪 Résultats

#### ✅ Sur maquette :
- Détection précise des IDs et vecteurs.

Détection sur maquette
*Fig. 3 : ArUco détectés sur la maquette.*

#### ✅ En conditions réelles :
- Bonne robustesse, même en présence d’ombres ou d’objets.

Détection terrain réel
*Fig. 4 : Détection fiable dans un environnement encombré.*

---

## 🗺️ 3. Positionnement & Cheminement

### 🧭 Détermination de la position initiale
- Les ArUco servent de repères pour définir l’origine.
- Transformation vers une **représentation 2D** exploitable.
- Discrétisation du terrain pour identifier les zones accessibles.

Position initiale
*Fig. 5 : Position initiale représentée en 2D.*

### 🔄 Suivi du mouvement
- Mises à jour dynamiques selon les vecteurs.
- Ajustement en cours sur l’estimation de la distance parcourue.

Mouvement du robot
*Fig. 6 : Mise à jour de la position du robot.*

---

## 🏗️ 4. Infrastructure : Tour Caméra

En attendant la structure finale de l’équipe mécanique, une **tour temporaire** a été fabriquée pour fixer la caméra.

Tour actuelle
*Fig. 7 : Structure provisoire pour la caméra.*

---

## 📈 5. Performances & Mesures

### 🎯 Objectif
Comparer la **position calculée** vs **position réelle** pour mesurer la précision du système.

### 📊 Résultats

- **Erreur moyenne** : ~ **1.8 cm**
- **Fréquence (FPS)** :
  - Setup normal : **3–4 FPS**
  - Setup optimisé : **10–12 FPS**

### 📉 Graphe de performance FPS (manquant dans version précédente)



*Fig. 8 : FPS du setup normal.*

---

## 🎥 6. Démonstration Vidéo

Une vidéo illustre le fonctionnement du système en temps réel, montrant la **réactivité** et la **précision** de la localisation :

➡️ [Lien vers la démonstration vidéo](https://github.com/user-attachments/assets/b6591760-27ca-40ef-97e6-4b8968a7495c)

---

## 🖼️ 7. Illustrations Complémentaires

**Détection des ArUco sur la maquette :**  


**Vue du terrain avec les ArUco visibles :**  


---

## ✅ 8. Conclusion & Roadmap

Le système est **fiable**, **réactif** et prêt pour une intégration complète dans le système de navigation.

### 🚀 Prochaines étapes :
- Améliorer l’estimation des distances.
- Générer une carte exploitable par **ROS** (niveaux de gris).
- Finaliser l'intégration ROS.
- Tests intensifs sur terrain réel.

---

### 👥 Équipe Vision
- **Khalid ZOUHAIR**
- **Mohamed EL KOURMISS**
- **Abderrahmane EL FELSOUFI**

---

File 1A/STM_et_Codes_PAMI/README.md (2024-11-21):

# Voici le Projet STM pour le PAMI Coupe de France 2425---- ENSEA ARES

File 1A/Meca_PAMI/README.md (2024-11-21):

# Hello ici c'est la meca

## déposer des .step

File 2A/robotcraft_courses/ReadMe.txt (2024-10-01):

--------- Introduction ---------

Les différents dossiers qui vont sont proposées regroupent l'ensemble des cours que Mateo, Antoine et Sammy ont eu l'opportunité d'assister à Robotcraft. Toutefois l'objectif de ce programme consistait surtout à l'apprentissage de ROS. 

Dans chaque dossier un fichier .txt résume l'ensemble du contenu du dossier.

L'organisation des dossiers est toujours la même : les cours sont au format .pdf et commencent avec le nom Craft_?_? le reste c'est de l'extra et/ou de la datasheet dans un dossier séparé "extra" (ce sont que des livres ou documents supplémentaires pour en connaître davantage tout simplement, toutefois il se pourrait que vous y trouvez des corrections d'exercice --ACTUELLEMENT INDISPONIBLE SUR LE GITHUB-- ).

--------- odométrie ---------

L'odométrie est expliquée dans le cours 4_2.

--------- ROS ---------

Tout ce qui concerne ROS commence à partir du cours 5 à savoir "Introduction to Linux".

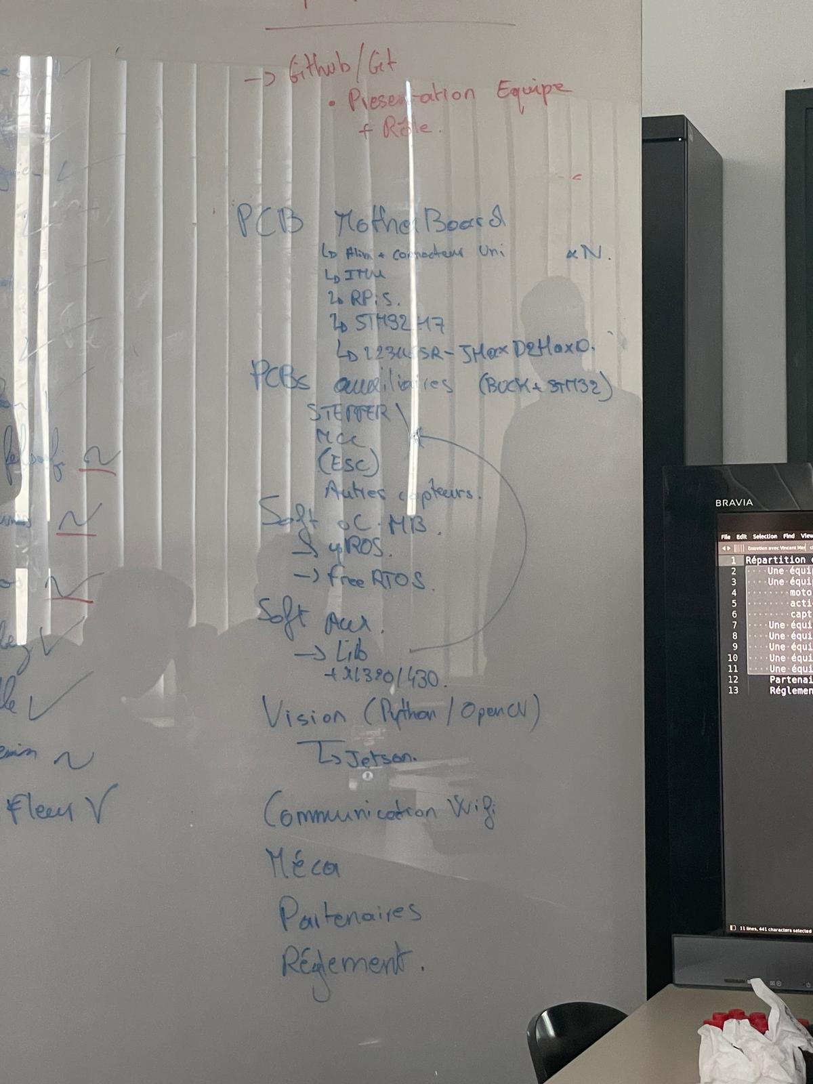
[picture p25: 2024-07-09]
2A/Hardware/Hardware_électronique/Docs/list_premier.jpeg

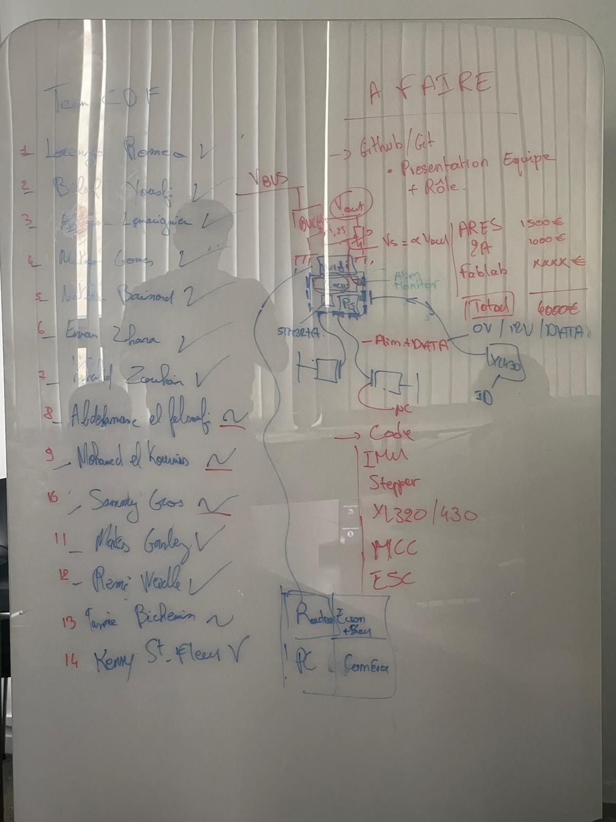
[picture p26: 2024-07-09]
2A/Hardware/Hardware_électronique/Docs/schéma_premier.jpeg

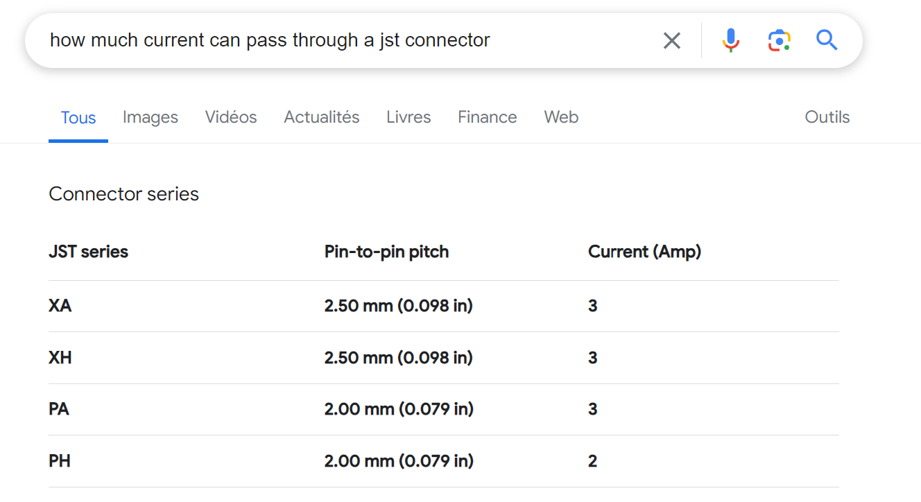
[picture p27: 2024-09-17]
2A/Hardware/Hardware_électronique/Docs/current_jst.png

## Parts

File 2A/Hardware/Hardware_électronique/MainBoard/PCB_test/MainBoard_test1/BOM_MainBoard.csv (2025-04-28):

Reference | Value | Datasheet | Footprint | Qty | DNP
ARU1 | 180G-2 |  | MainBoard:180G-2 | 1
BT1 | Battery | ~ | Connector_AMASS:AMASS_XT60PW-F_1x02_P7.20mm_Horizontal | 1
C1 | 220u | https://fr.rs-online.com/web/p/kits-de-condensateurs/2120543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 | Capacitor_SMD:CP_Elec_10x10.5 | 1
C2,C7,C29,C37 | 10u | -- valeurs mixtées -- | -- valeurs mixtées -- | 4
C3 | 2.2n |  | Capacitor_SMD:C_0402_1005Metric | 1
C4,C6,C8,C38 | 22u | ~ | Capacitor_SMD:C_0402_1005Metric | 4
C5,C12,C13,C14,C15,C16,C17,C18,C19,C20,C21,C22,C23,C24,C25,C26,C27,C28,C35,C36,C39,C40,C41 | 100n | ~ | Capacitor_SMD:C_0402_1005Metric | 23
C30,C31,C32,C33 | 10n | ~ | Capacitor_SMD:C_0402_1005Metric | 4
C34,C45,C46,C47 | 1u | ~ | Capacitor_SMD:C_0402_1005Metric | 4
C42,C43,C44 | 2.2u | ~ | Capacitor_SMD:C_0402_1005Metric | 3
D1,D2,D3,D4,D5,D6,D7,D8,D9,D22 | ESD7C5.0DT5G | https://www.mouser.fr/datasheet/2/308/1/ESD7C3_3D_D-2311593.pdf | Package_TO_SOT_SMD:SOT-416 | 10
D10 | 1.5SMBJ36CA | https://www.mouser.fr/datasheet/2/54/BOURNS_1_5SMBJ_datasheet-2530221.pdf | Diode_SMD:D_SMB | 1
D11 | 4V7 | https://www.mouser.fr/datasheet/2/916/BZX84J_SER-1319442.pdf | Diode_SMD:D_0603_1608Metric | 1
D18,D19,D20,D21 | Blue LED | ~ | LED_SMD:LED_0603_1608Metric | 4
F1 | 15A | https://www.mouser.fr/datasheet/2/643/ds_CP_0685P_series-1960388.pdf | Fuse:Fuse_1206_3216Metric | 1
J2 | Conn_ST_STDC14 | https://www.st.com/content/ccc/resource/technical/document/user_manual/group1/99/49/91/b6/b2/3a/46/e5/DM00526767/files/DM00526767.pdf/jcr:content/translations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 | Connector_PinHeader_1.27mm:PinHeader_2x07_P1.27mm_Vertical_SMD | 1
J3 | Conn_02x10_Odd_Even | ~ | Connector_PinSocket_2.54mm:PinSocket_2x10_P2.54mm_Vertical | 1
L1 | 4.7u | https://www.mouser.fr/datasheet/2/447/P890-2902881.pdf | MainBoard:PA5432.472NLT | 1
L3 | 39n | ~ | Inductor_SMD:L_0603_1608Metric | 1
LIDAR1,UART1,UART2,UART3,UART4,UART5,UART6,UART7,UART8,UART10 | Conn_01x04_Male | ~ | Connector_JST:JST_EH_B4B-EH-A_1x04_P2.50mm_Vertical | 10
Q1 | PMOS | https://www.onsemi.com/pdf/datasheet/nttfs015p03p8z-d.pdf | MainBoard:MOS_WDFN8 | 1
R1,R12,R13,R14,R15,R16,R17,R18,R19 | 10k | ~ | Resistor_SMD:R_0402_1005Metric | 9
R2 | 200k | ~ | Resistor_SMD:R_0402_1005Metric | 1
R3 | 19.6k | ~ | Resistor_SMD:R_0402_1005Metric | 1
R5 | 36k | ~ | Resistor_SMD:R_0402_1005Metric | 1
R6 | 6.8k | ~ | Resistor_SMD:R_0402_1005Metric | 1
R20,R21,R22,R23 | 390 | ~ | Resistor_SMD:R_0402_1005Metric | 4
SW1,SW2,SW3,SW4 | SW_Push | ~ | MainBoard:435451019820 | 4
TP1,TP3,TP5 | TestPoint | ~ | TestPoint:TestPoint_Pad_D2.0mm | 3
U1 | STM32H735IGTx | https://www.st.com/resource/en/datasheet/stm32h735ig.pdf | Package_QFP:LQFP-176_24x24mm_P0.5mm | 1
U3 | ~ | https://www.mouser.fr/datasheet/2/115/DIOD_S_A0011818526_1-2543600.pdf | Package_SO:SOIC-8-1EP_3.9x4.9mm_P1.27mm_EP2.95x4.9mm_Mask2.71x3.4mm | 1
U4 | AZ1117-3.3 | https://www.diodes.com/assets/Datasheets/AZ1117.pdf | Package_TO_SOT_SMD:SOT-223-3_TabPin2 | 1

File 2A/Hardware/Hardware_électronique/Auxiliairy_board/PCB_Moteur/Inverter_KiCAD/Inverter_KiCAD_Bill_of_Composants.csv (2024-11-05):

Reference | Value | Datasheet | Footprint | Qty | Magasin
BT1 | Battery | ~ | Connector_AMASS:AMASS_XT60-M_1x02_P7.20mm_Vertical | 1 | https://www.conrad.fr/fr/p/reely-re-6586515-fiche-male-pour-batterie-xt60-3-5-mm-a-souder-1-pc-s-2195505.html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
C1,C4,C17,C23,C33 | 10u | -- valeurs mixtées -- | Capacitor_SMD:C_0603_1608Metric_Pad1.08x0.95mm_HandSolder | 5
C2,C3,C25 | 1u | ~ | Capacitor_SMD:C_0603_1608Metric_Pad1.08x0.95mm_HandSolder | 3
C5,C6,C7,C13,C14,C15 | 4.7n | ~ | Capacitor_SMD:C_0402_1005Metric | 6
C8,C9,C10 | 220u | https://www.we-online.com/components/products/datasheet/865060657012.pdf | Capacitor_SMD:CP_Elec_10x10.5 | 3 | https://fr.farnell.com/c/composants-passifs/condensateurs/condensateurs-electrolytiques-aluminium/condensateurs-electrolytiques-aluminium-cms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
C16,C20,C31,C38,C39 | 10n | ~ | Capacitor_SMD:C_0402_1005Metric | 5
C18 | 22u | ~ | Capacitor_SMD:C_0603_1608Metric_Pad1.08x0.95mm_HandSolder | 1 | https://www.we-online.com/en/components/products/WCAP-CSGP-10VDC?sq=885012106032#885012106032
C19,C24,C26,C27,C28,C29,C30,C32,C1201 | 100n | ~ | Capacitor_SMD:C_0402_1005Metric | 9
C21,C22 | 22p | ~ | Capacitor_SMD:C_0402_1005Metric | 2
C34 | 4.7nF | ~ | Capacitor_SMD:C_0402_1005Metric_Pad0.74x0.62mm_HandSolder | 1
C35 | 22nF | ~ | Capacitor_SMD:C_0402_1005Metric | 1
C36 | 47u | ~ | Capacitor_SMD:C_0805_2012Metric | 1 | https://fr.farnell.com/taiyo-yuden/lmk212bbj476mg-t/cap-47uf-10v-mlcc-0805/dp/3217585
Converter_DCDC_WPMDH1302401 | ~ |  | Package_TO_SOT_SMD:TO-263-7_TabPin8 | 1 | https://www.we-online.com/en/components/products/MAGIC-VDRM#171032401
D1,D3,D4,D5,D6,D7,D8 | Red LED | ~ | LED_SMD:LED_0603_1608Metric | 7
D9,D10,D11,D12 | Blue LED | ~ | LED_SMD:LED_0603_1608Metric | 4
J1 | Conn_02x02_Top_Bottom | ~ | Connector_Molex:Molex_Micro-Fit_3.0_43045-0400_2x02_P3.00mm_Horizontal | 1 | https://www.digikey.fr/fr/products/detail/molex/0039012040/61376?productid=61376&gad_source=5
J2 | 173010542 | https://www.we-online.com/components/products/datasheet/173010542.pdf | Connector_PinHeader_2.54mm:PinHeader_1x03_P2.54mm_Vertical | 1
J3 | Conn_02x05_Odd_Even | ~ | Connector_PinHeader_2.54mm:PinHeader_2x05_P2.54mm_Vertical | 1
J4,J5 | Conn_01x02 | ~ | Connector_JST:JST_XH_B2B-XH-A_1x02_P2.50mm_Vertical | 2
J6 | Conn_ST_STDC14 | https://www.st.com/content/ccc/resource/technical/document/user_manual/group1/99/49/91/b6/b2/3a/46/e5/DM00526767/files/DM00526767.pdf/jcr:content/translations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 | Connector_PinHeader_1.27mm:PinHeader_2x07_P1.27mm_Vertical_SMD | 1
J7 | Conn_01x04_Pin | ~ | Connector_JST:JST_XH_B4B-XH-A_1x04_P2.50mm_Vertical | 1
L1 | 39n | ~ | Inductor_SMD:L_0603_1608Metric | 1
Q5 | SQ2310ES | ~ | Package_TO_SOT_SMD:SOT-23 | 1
R1,R4,R7,R8,R10,R18,R19,R20,R21 | 390 | ~ | Resistor_SMD:R_0402_1005Metric | 9
R3 | 100k | ~ | Resistor_SMD:R_0402_1005Metric | 1
R5 | 8.2K | ~ | Resistor_SMD:R_0402_1005Metric | 1
R6 | 2k7 | ~ | Resistor_SMD:R_0402_1005Metric | 1
R9 | 680 | ~ | Resistor_SMD:R_0402_1005Metric | 1
R11 | 22 | ~ | Resistor_SMD:R_0402_1005Metric | 1
R12,R13,R14,R15,R16,R17,R22,R23,R24,R25 | 10k | ~ | Resistor_SMD:R_0402_1005Metric | 10
R26 | 100k | ~ | Resistor_SMD:R_0402_1005Metric | 1
R27 | 1.91k | ~ | Resistor_SMD:R_0402_1005Metric | 1
R28 | 34k | ~ | Resistor_SMD:R_0402_1005Metric | 1
R1201 | 200 | ~ | Resistor_SMD:R_0402_1005Metric | 1
SW1,SW2,SW7,SW8 | SW_Push | ~ | Custom:435451019820 | 4
TP1,TP2,TP3,TP4 | TestPoint | ~ | TestPoint:TestPoint_Pad_D2.0mm | 4
U1 | MIC4606 | https://www.mouser.fr/datasheet/2/268/MIC4606_85V_Full_Bridge_MOSFET_Drivers_with_Adapti-3442103.pdf | Package_SO:TSSOP-16-1EP_4.4x5mm_P0.65mm_EP3x3mm | 1 | https://www.mouser.fr/ProductDetail/Microchip-Technology/MIC4606-2YTS-TR?qs=fxR7EJxuiMGiGNq6G0IdXQ%3D%3D
U2,U3 | GO 10-SME/SP3 | GO 10-SME | Custom:SOIC8-GO-SME&slash_SP3_LEM | 2
U4 | AZ1117-3.3 | https://www.diodes.com/assets/Datasheets/AZ1117.pdf | Package_TO_SOT_SMD:SOT-223-3_TabPin2 | 1
U5 | MAX3097ECSE+ | https://www.mouser.fr/datasheet/2/609/MAX3097E_MAX3098E-3128450.pdf | Package_SO:SOIC-16_3.9x9.9mm_P1.27mm | 1
U6 | STM32G474RETx | https://www.st.com/resource/en/datasheet/stm32g474re.pdf | Package_QFP:LQFP-64_10x10mm_P0.5mm | 1
U7,U8 | CSD86350Q5D | CSD86350Q5D | CSD87351Q5D:DQY0008A | 2 | https://www.mouser.fr/ProductDetail/Texas-Instruments/CSD86350Q5D?qs=6mL4zoXrlH82elBdFmujUQ%3D%3D
U1201 | TCN75A | https://docs.rs-online.com/fc92/0900766b80d0dfb5.pdf | Package_SO:SOIC-8_3.9x4.9mm_P1.27mm | 1
Y1 | 16M | https://4donline.ihs.com/images/VipMasterIC/IC/ABRC/ABRCS03441/ABRCS03441-1.pdf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 | Custom:ABLS-7.3728MHZ-CL-RESR-A-1-G-F | 1

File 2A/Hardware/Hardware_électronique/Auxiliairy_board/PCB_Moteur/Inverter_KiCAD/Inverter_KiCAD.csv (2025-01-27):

Source: | /home/nicolas/git/AAP_ENSEA_Inverter/Inverter_KiCAD/Inverter_KiCAD.kicad_sch
Date: | lun. 18 sept. 2023 08:32:15
Tool: | Eeschema 7.0.7-7.0.7~ubuntu22.04.1
Generator: | /usr/share/kicad/plugins/bom_csv_grouped_by_value.py
Component Count: | 220
Collated Components:
Item | Qty | Reference(s) | Value | LibPart | Footprint | Datasheet | DNP | Fournisseur | MFR | Ref | URL | Vmax
1 | 6 | C201, C202, C301, C302, C401, C402 | 100u | Device:C_Polarized | Capacitor_SMD:CP_Elec_6.3x7.7 | ~ |  | Wurth | 865 060 445 005 |  |  | 25V
2 | 7 | C203, C204, C303, C304, C403, C404, C502 | 22u | Device:C_Polarized | Capacitor_SMD:CP_Elec_5x5.4 | ~ |  | Wurth | 865 060 442 002 |  |  | 25V
3 | 4 | C205, C305, C405, C604 | 10n | Device:C_Small | Capacitor_SMD:C_0402_1005Metric | ~ |  | Wurth | 885 012 205 050
4 | 3 | C206, C306, C406 | 10u | Device:C_Small | Capacitor_SMD:C_2220_5650Metric | https://www.we-online.com/components/products/datasheet/885012214001.pdf |  | Wurth | 885 012 214 001 |  | https://www.we-online.com/components/products/datasheet/885012214001.pdf
5 | 24 | C207, C208, C307, C308, C407, C408, C605, C606, C804, C807, C808, C809, C810, C811, C812, C814, C815, C816, C817, C818, C901, C902, C1201, C1301 | 100n | Device:C_Small | Capacitor_SMD:C_0402_1005Metric | ~ |  | Wurth | 885 012 105 018
6 | 12 | C209, C210, C211, C309, C310, C311, C409, C410, C411, C601, C602, C603 | 4.7n | Device:C_Small | Capacitor_SMD:C_0402_1005Metric | ~ |  | Wurth | 885 012 205 048
7 | 1 | C501 | 10u | Device:C_Polarized | Capacitor_SMD:CP_Elec_4x5.4 | ~ |  | Wurth | 865 060 440 001
8 | 2 | C801, C802 | 22p | Device:C_Small | Capacitor_SMD:C_0402_1005Metric | ~ |  | Wurth | 885 012 005 009
9 | 3 | C803, C806, C813 | 10u | Device:C_Small | Capacitor_SMD:C_0603_1608Metric | ~ |  | Wurth | 885 012 106 006
10 | 2 | C805, C903 | 1u | Device:C_Small | Capacitor_SMD:C_0402_1005Metric | ~ |  | Wurth | 885 012 105 012
11 | 1 | C904 | 1n | Device:C_Small | Capacitor_SMD:C_0402_1005Metric | ~ |  | Wurth | 885 012 205 044
12 | 5 | C1001, C1002, C1003, C1004, C1005 | 1.5m | Device:C_Polarized | Capacitor_THT:CP_Radial_D35.0mm_P10.00mm_SnapIn | ~ |  | Wurth | 861 011 086 027
13 | 3 | D201, D301, D401 | Green LED | Device:LED | LED_SMD:LED_0603_1608Metric | ~ |  | Wurth | 150 060 GS5 504 0
14 | 12 | D202, D203, D302, D303, D402, D403, D501, D502, D503, D1401, D1402, D1403 | Red LED | Device:LED | LED_SMD:LED_0603_1608Metric | ~ |  | Wurth | 150 060 RS5 504 0
15 | 4 | D801, D802, D803, D804 | Blue LED | Device:LED | LED_SMD:LED_0603_1608Metric | ~ |  | Wurth | 150 060 BS5 504 0
16 | 1 | D901 | Red LED | Device:LED_Small | LED_SMD:LED_0603_1608Metric | ~ |  | Wurth | 150 060 RS5 504 0
17 | 2 | D902, D903 | VS-15TQ060S-M3 | Device:D_Schottky | Package_TO_SOT_SMD:TO-263-2 | https://www.vishay.com/docs/94927/vs-15tq060s-m3.pdf |  | Farnell | VS-15TQ060S-M3 | 2909608
18 | 1 | F501 | Fuse | Device:Fuse | Custom:0031.8201 | ~ |  | Wurth | 696 108 003 002
19 | 14 | H101, H102, H103, H104, H105, H106, H107, H108, H109, H110, H111, H112, H113, H114 | MountingHole_Pad | Mechanical:MountingHole_Pad | MountingHole:MountingHole_3.2mm_M3_Pad_Via | ~ |  |  | -
20 | 2 | J101, J103 | Conn_02x19_Odd_Even | Connector_Generic:Conn_02x19_Odd_Even | Connector_PinHeader_2.54mm:PinHeader_2x19_P2.54mm_Vertical | ~ |  | Farnell | SSW-119-01-T-D | 2667437
21 | 2 | J102, J901 | Conn_01x02 | Connector_Generic:Conn_01x02 | Custom:691311500102 | https://www.we-online.com/components/products/datasheet/691311500102.pdf |  | Wurth | 691 311 700 102
22 | 1 | J104 | Conn_01x03 | Connector_Generic:Conn_01x03 | Custom:691311500103 | https://www.we-online.com/components/products/datasheet/691311500103.pdf |  | Wurth | 691 311 700 103
23 | 1 | J501 | PX0580-PC-12132 | PX0580-PC-12132:PX0580-PC-12132 | Custom:PX0580-PC-12132 | PX0580-PC-12132 |  | RS | PX0580/PC/12132 | 261-5840
24 | 1 | J801 | USB_C_Receptacle_USB2.0 | Connector:USB_C_Receptacle_USB2.0 | Connector_USB:USB_C_Receptacle_HRO_TYPE-C-31-M-12 | https://www.usb.org/sites/default/files/documents/usb_type-c.zip |  | Wurth | 629 722 000 214
25 | 1 | J802 | Conn_01x05 | Connector_Generic:Conn_01x05 | Connector_JST:JST_XH_B5B-XH-A_1x05_P2.50mm_Vertical | ~ |  | Stock
26 | 1 | J803 | Conn_ST_STDC14 | Connector:Conn_ST_STDC14 | Connector_PinHeader_1.27mm:PinHeader_2x07_P1.27mm_Vertical_SMD | https://www.st.com/content/ccc/resource/technical/document/user_manual/group1/99/49/91/b6/b2/3a/46/e5/DM00526767/files/DM00526767.pdf/jcr:content/translations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 |  | Stock
27 | 1 | J804 | Conn_01x04 | Connector_Generic:Conn_01x04 | Connector_JST:JST_XH_B4B-XH-A_1x04_P2.50mm_Vertical | ~ |  | Stock
28 | 2 | J1101, J1102 | Conn_01x02 | Connector_Generic:Conn_01x02 | Connector_JST:JST_XH_B2B-XH-A_1x02_P2.50mm_Vertical | ~ |  | Stock
29 | 1 | J1301 | DE9_Receptacle_MountingHoles | Connector:DE9_Receptacle_MountingHoles | Custom:618009233821 | https://www.we-online.com/components/products/datasheet/618009231421.pdf |  | Wurth | 618 009 231 421
30 | 1 | L801 | 39n | Device:L_Small | Inductor_SMD:L_0603_1608Metric | ~ |  | Wurth | 744 786 013 9
31 | 3 | Q201, Q301, Q401 | HCPL-315J-500E | Custom:HCPL-315J-500E | Custom:SO-16_HCPL-315J_BRA | HCPL-315J-500E |  | RS | HCPL-315J-500E | 174-4163
32 | 6 | Q202, Q203, Q302, Q303, Q402, Q403 | IRF540N | Transistor_FET:IRF540N | Package_TO_SOT_THT:TO-220-3_Vertical | http://www.irf.com/product-info/datasheets/data/irf540n.pdf |  | RS | IRF540NPBF | 914-8154
33 | 1 | Q901 | BUK9637-100E | Transistor_FET:IRFS4229 | Package_TO_SOT_SMD:TO-263-2 | https://www.infineon.com/dgdl/irfs4229pbf.pdf?fileId=5546d462533600a401535639fdc421a1 |  | Farnell | BUK9637-100E,118 | 2254193
34 | 1 | Q1101 | SQ2310ES | Device:Q_NMOS_GSD | Package_TO_SOT_SMD:SOT-23 | ~ |  | RS | SQ2310ES-T1_BE3 | 787-9443
35 | 6 | R201, R202, R301, R302, R401, R402 | 170 | Device:R_Small | Resistor_SMD:R_0402_1005Metric | ~ |  | Stock
36 | 15 | R203, R204, R205, R303, R304, R305, R403, R404, R405, R503, R804, R805, R806, R807, R901 | 390 | Device:R_Small | Resistor_SMD:R_0402_1005Metric | ~ |  | Farnell | CRCW0402390RFKEDC | 4177482
37 | 6 | R206, R208, R306, R308, R406, R408 | 30 | Device:R_Small | Resistor_SMD:R_1206_3216Metric | ~ |  | Stock
38 | 14 | R207, R209, R307, R309, R407, R409, R801, R808, R809, R810, R902, R1401, R1402, R1403 | 10k | Device:R_Small | Resistor_SMD:R_0402_1005Metric | ~ |  | Farnell | MC00625W0402110K | 2130433
39 | 4 | R210, R310, R410, R601 | 160k | Device:R_Small | Resistor_SMD:R_0402_1005Metric | ~ |  | Stock
40 | 4 | R211, R311, R411, R602 | 1k | Device:R_Small | Resistor_SMD:R_0402_1005Metric | ~ |  | Farnell | MCWR04X1001FTL | 2446437
41 | 1 | R501 | 2k7 | Device:R_Small | Resistor_SMD:R_0402_1005Metric | ~ |  | Stock
42 | 1 | R502 | 680 | Device:R_Small | Resistor_SMD:R_0402_1005Metric | ~ |  | Stock
43 | 1 | R701 | 27k | Device:R_Small | Resistor_SMD:R_0402_1005Metric | ~ |  | Stock
44 | 2 | R802, R803 | 5.1k | Device:R_Small | Resistor_SMD:R_0402_1005Metric | ~ |  | Sotck
45 | 1 | R903 | 4.7 | Device:R_Small | Resistor_SMD:R_1206_3216Metric | ~ |  | Stock
46 | 1 | R1101 | 22 | Device:R_Small | Resistor_SMD:R_0402_1005Metric | ~ |  | Stock
47 | 1 | R1102 | 10k | Device:R_Small_US | Resistor_SMD:R_0402_1005Metric | ~ |  | Farnell | MC00625W0402110K | 2130433
48 | 1 | R1201 | 200 | Device:R_Small | Resistor_SMD:R_0402_1005Metric | ~ |  | Stock
49 | 5 | SW801, SW802, SW803, SW804, SW805 | SW_Push | Switch:SW_Push | Custom:435451019820 | ~ |  | Wurth | 435 451 019 820
50 | 3 | U201, U301, U401 | MPRB2415S-6W | Custom:MPRB2415S-6W | Custom:MPRB2415S |  |  | Farnell* | MPRB2415S/PQQ6W-Q24-D15-S | 3652723/4138610
51 | 3 | U202, U302, U402 | MPRB2415S-6W | :MPRB2415S-6W_1 | Custom:MPRB2415S |  |  | Farnell* | MPRB2415S/PQQ6W-Q24-D15-S | 3652723/4138610
52 | 4 | U203, U303, U403, U602 | HCPL-7800-500E | Custom:HCPL-7800-500E | Custom:DIP-8 Gull Wing |  |  | RS | HCPL-7800A-500E | 174-4179
53 | 4 | U204, U304, U404, U601 | GO 10-SME/SP3 | Custom:GO_10-SME | Custom:SOIC8-GO-SME&slash_SP3_LEM | GO 10-SME |  | Farnell | GO 10-SME/SP3 | 3796461
54 | 1 | U501 | MP-LD30-23B12R2 | MP-LD30-23B15R2:MP-LD30-23B12R2 | Custom:MP-LD30-23B15R2 | MP-LD30-23B12R2 |  | Farnell | MP-LD30-23B15R2 | 3780527
55 | 1 | U502 | 173010542 | Custom:173010542 | Custom:173010578 | 173010542 |  | Wurth | 173 010 542
56 | 1 | U503 | AZ1117-3.3 | Regulator_Linear:AZ1117-3.3 | Package_TO_SOT_SMD:SOT-223-3_TabPin2 | https://www.diodes.com/assets/Datasheets/AZ1117.pdf |  | RS | AZ1117H-3.3TRE1 | 921-0701
57 | 1 | U701 | 17791063215 | Custom:17791063215 | Custom:17791063215 | https://www.we-online.com/components/products/datasheet/17791063215.pdf |  | Wurth | 177 910 632 15
58 | 1 | U801 | STM32G474RETx | MCU_ST_STM32G4:STM32G474RETx | Package_QFP:LQFP-64_10x10mm_P0.5mm | https://www.st.com/resource/en/datasheet/stm32g474re.pdf |  | RS | STM32G474RET6 | 193-9861
59 | 1 | U802 | USBLC6-2SC6 | Power_Protection:USBLC6-2SC6 | Package_TO_SOT_SMD:SOT-23-6 | https://www.st.com/resource/en/datasheet/usblc6-2.pdf |  | RS | USBLC6-2SC6 | 624-7693
60 | 1 | U901 | ACPL-077L | Custom:ACPL-077L | Package_SO:SO-8_3.9x4.9mm_P1.27mm |  |  | RS | ACPL-077L-500E | 230-5293
61 | 1 | U902 | TC1412 | Custom:TC1412 | Package_SO:SOIC-8_3.9x4.9mm_P1.27mm |  |  | RS | TC1412NEOA | 1834898
62 | 1 | U1201 | TCN75A | Custom:TCN75A | Package_SO:SOIC-8_3.9x4.9mm_P1.27mm | https://docs.rs-online.com/fc92/0900766b80d0dfb5.pdf |  | RS | TCN75AVOA | 738-6014
63 | 1 | U1301 | MAX3097ECSE+ | Custom:MAX3097ECSE+ | Package_SO:SOIC-16_3.9x9.9mm_P1.27mm | https://www.mouser.fr/datasheet/2/609/MAX3097E_MAX3098E-3128450.pdf |  | Farnell | MAX3097ECSE+ | 2518786
64 | 1 | Y801 | 16M | Device:Crystal | Custom:ABLS-7.3728MHZ-CL-RESR-A-1-G-F | https://4donline.ihs.com/images/VipMasterIC/IC/ABRC/ABRCS03441/ABRCS03441-1.pdf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 |  | Farnell | ABLS-16.000MHZ-20-B-3-H-T | 3228387

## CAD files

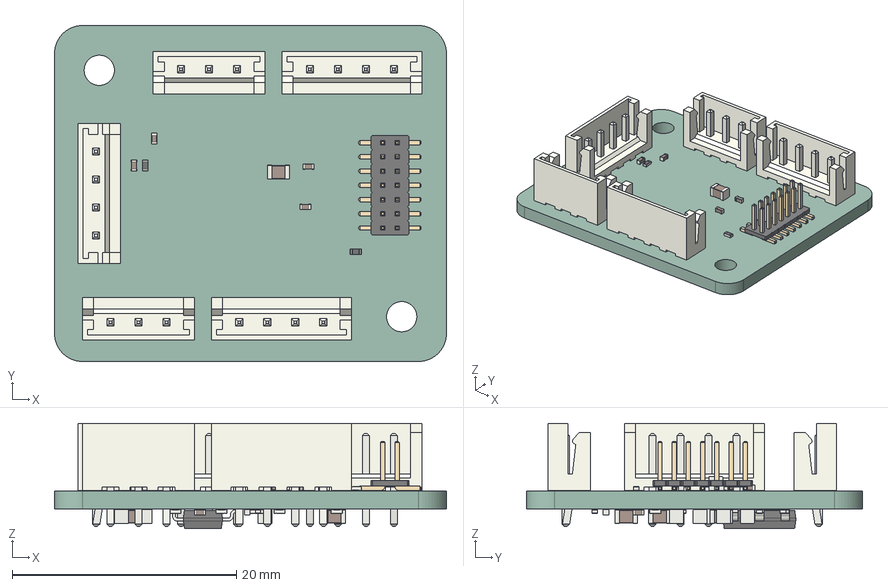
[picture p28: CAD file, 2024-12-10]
2A/Hardware/Hardware_électronique/Auxiliairy_board/PCB_Stepper/Stepper.step
35.0 x 30.0 x 9.40 mm
R_0402_1005Metric x 13
C_0402_1005Metric x 6
C_0805_2012Metric x 9
PinHeader_2x07_P127mm_Vertical_SMD
JST_B4B_EH_A x 3
JST_B3B_EH_A x 2
SOT_223
Stepper_PCB

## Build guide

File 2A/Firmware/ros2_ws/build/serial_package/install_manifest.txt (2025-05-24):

/home/carpe-bleue/ros2_ws/install/serial_package/lib/serial_package/tirette
/home/carpe-bleue/ros2_ws/install/serial_package/lib/serial_package/bag_player_node
/home/carpe-bleue/ros2_ws/install/serial_package/lib/serial_package/bag_listener

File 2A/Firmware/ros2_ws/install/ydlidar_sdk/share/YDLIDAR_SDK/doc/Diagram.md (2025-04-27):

# FlowChart

```flow
st=>start: Start
op=>operation: Set Paramamters and Initialize
op1=>operation: TrunOn
tr=>operation: Try Again
op2=>operation: doProcessSimple
op3=>operation: TrunOff
op4=>operation: disconnecting
cond=>condition: success Yes or No?
cond1=>condition: success Yes or No?
cond2=>condition: success Yes or No?
cond3=>condition: LOOP Yes or No?
cond4=>condition: TryAgain Yes or No?
e=>end: End
en=>end: End

st(left)->op->cond
cond(yes)->op1->cond1
cond(no)->op3->op4->e
cond1(yes)->op2->cond3
cond3(yes)->op2
cond3(no, left)->op3->op4->e
cond1(no,right)->tr(bottom)->cond4
cond4(yes)->op3
cond4(no)->op3(right)->op4(right)->e
```

# sequenceDiagram

```mermaid
sequenceDiagram
note over UserProgram: Set Paramters
note over UserProgram: Initialize SDK
UserProgram->Command: Get LiDAR Information
Command-->UserProgram: Device connected and Devce Information recevied
note over UserProgram: TurnOn
UserProgram->Command: Start LiDAR 
Command-->UserProgram: LiDAR Started successfully
UserProgram->LaserScan: Get Laser Scan Data
LaserScan-->UserProgram:  Laser Scan Data Recvied
note over UserProgram: doProcessSimple
loop Laser Scan Data
  LaserScan->UserProgram: doProcessSimple
end
note over UserProgram: TurnOff
UserProgram->Command: TurnOff 
note over UserProgram: disconnecting
UserProgram->Command: disconnecting
```

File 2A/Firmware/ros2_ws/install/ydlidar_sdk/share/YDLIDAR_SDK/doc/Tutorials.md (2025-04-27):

# YDLIDAR SDK Tutorials

Non-Beginners: If you're already familiar enough with YDLIDAR SDK, you can go through more in-depth SDK tutorial here. However, going over all basic Beginner Level tutorials is still recommended for all users to get exposed to new features.

If you are new to Linux/windows: You may find it helpful to first do a quick tutorial on common command line tools for linux/windows. A good one is here. 

# Table of Contents
- [Beginner Level](#Beginner-level)
    - [Writing a Simple Lidar Turorial (C++)](#writing-a-simple-lidar-tutorial-(c++))
    - [Writing a Simple Lidar Network Adapter Turorial (C++)](#writing-a-simple-lidar-network-adapter-tutorial-(c++))
    - [Writing a Simple Lidar Turorial (Python)](#writing-a-simple-lidar-tutorial-(python))
    - [Writing a Simple Lidar Turorial (C)](#writing-a-simple-lidar-tutorial-(c))
    - [Examining the simple lidar tutorial](#examining-the-simple-lidar-tutorial)

## Beginner Level
### [Writing a Simple Lidar Tutorial (C++)](tutorials/writing_lidar_tutorial_c++.md)
This tutorial covers how to write a lidar tutorial in C++. 
### [Writing a Simple Lidar Network Adapter Tutorial (C++)](tutorials/writing_lidar_network_adapter_tutorial_c++.md)
This tutorial covers how to write a lidar network adapter tutorial in C++. 
### [Writing a Simple Lidar Tutorial (Python)](tutorials/writing_lidar_tutorial_python.md)
This tutorial covers how to write a lidar tutorial in Python. 
### [Writing a Simple Lidar Tutorial (C)](tutorials/writing_lidar_tutorial_c.md)
This tutorial covers how to write a lidar tutorial in C. 
### [Examining the simple lidar tutorial](tutorials/examine_the_simple_lidar_tutorial.md)
This tutorial examines running the lidar tutorial.

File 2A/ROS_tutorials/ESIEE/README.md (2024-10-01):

# TD de ROS

- TD prise en main des outils ROS Turtlesim : https://perso.esiee.fr/~hamouchr/el3007/td/
- TD2 Turtlesim : publisher/subscriber : https://perso.esiee.fr/~hamouchr/el3007/td2/
- Mini-projet : pilotage de robot différentiel : https://perso.esiee.fr/~hamouchr/el3007/projet/

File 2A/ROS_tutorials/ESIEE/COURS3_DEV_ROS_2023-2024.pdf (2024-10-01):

18/03/2024

1

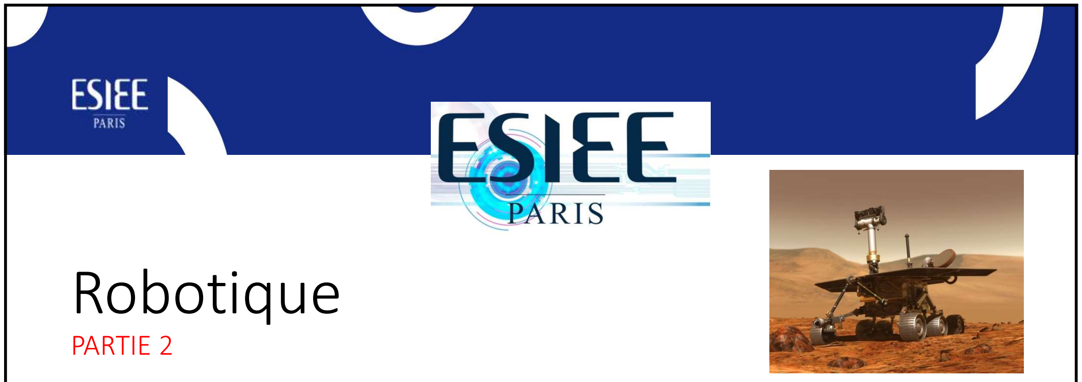
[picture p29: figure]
Robotique; PARTIE 2

Présentation ESIEE
Paris

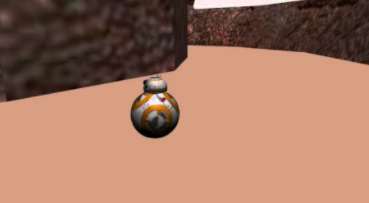
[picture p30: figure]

EL 3007

# R. HAMOUCHE r.hamouche@esiee.fr

2023-2024

# CRÉER DES APPLICATIONS ROS

ESIEE | 2

1

2

# Les librairies roscpp

Duration | Time | http://wiki.ros.org/APIs

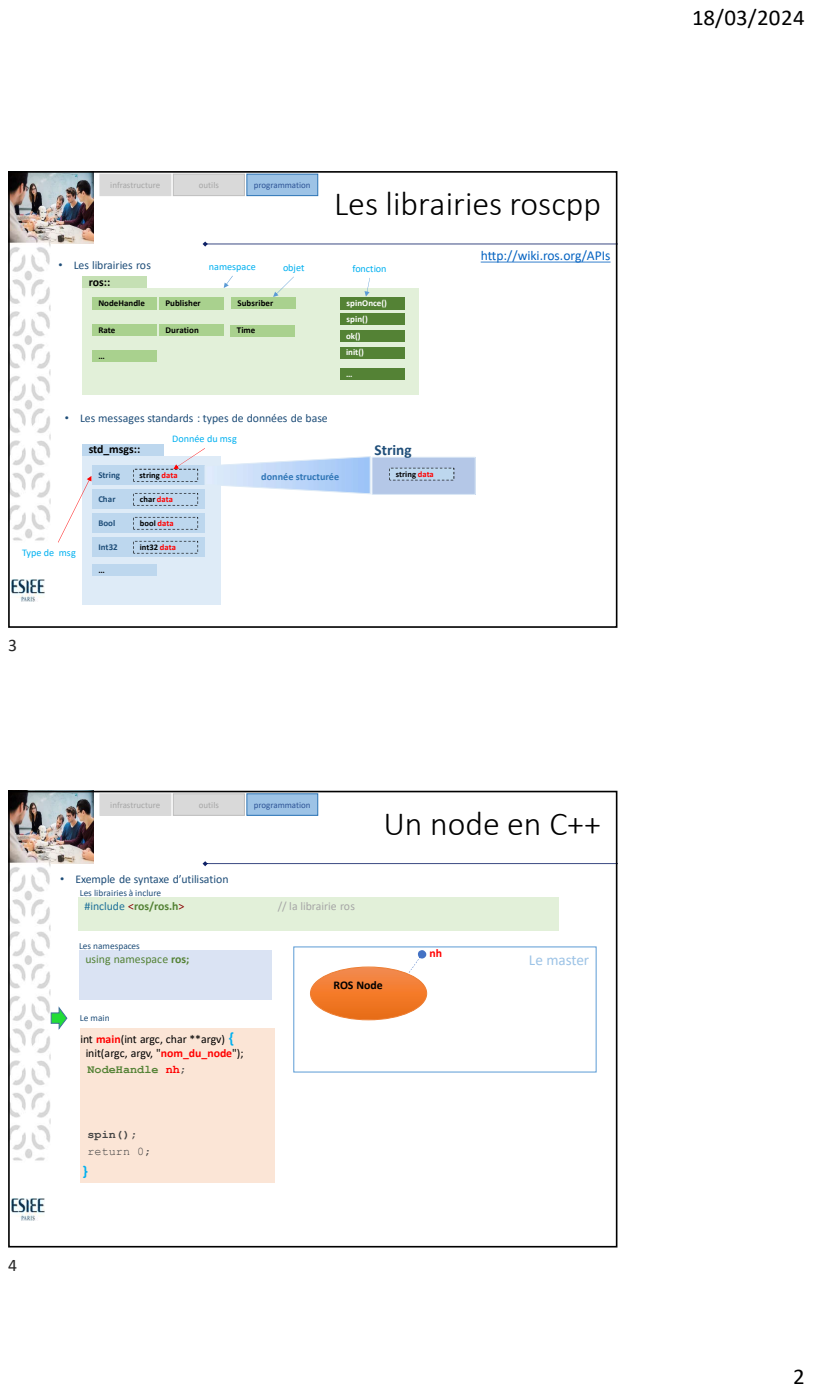
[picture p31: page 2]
infrastructure; outils; programmation • Les librairies ros; NodeHandle; Publisher ros::; Subsriber; String std_msgs::; spinOnce() spin(); string data; Char; char data; Bool; bool data; Int32; int32 data; String; namespace; objet; fonction; programmation #include <ros/ros.h>; // la librairie ros; Les namespaces; spin(); return 0; }; ROS Node

Rate
init() • Les messages standards : types de données de base

Donnée du msg

string data donnée structurée

Type de msg

Un node en C++

• Exemple de syntaxe d’utilisation
Les librairies à inclure using namespace ros;

Le master nh

Le main
int main(int argc, char **argv) {
init(argc, argv, "nom_du_node");
NodeHandle nh;

# Un message String

## String

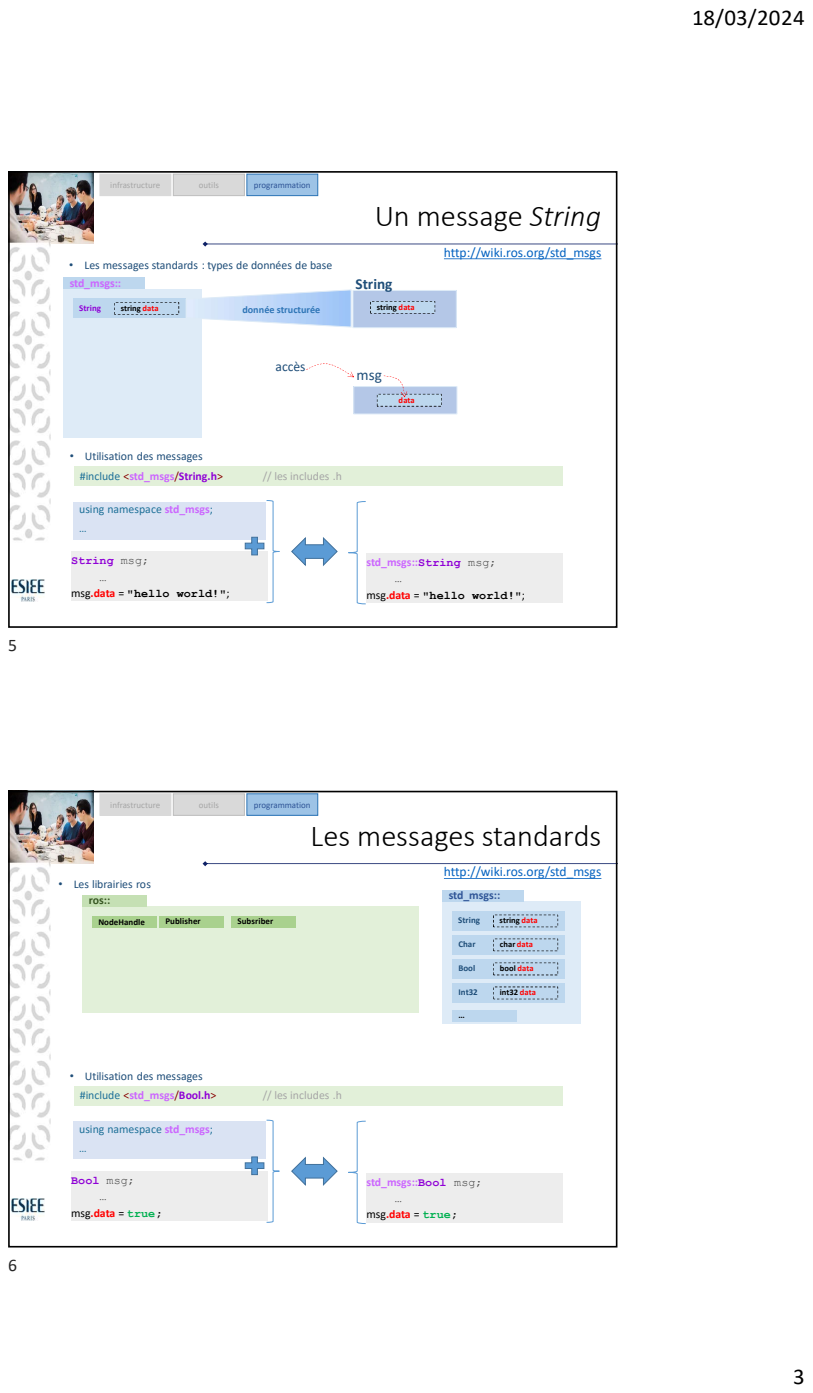
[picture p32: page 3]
infrastructure; outils; programmation; String msg;; … msg.data = "hello world!";; std_msgs::String msg;; #include <std_msgs/String.h>; // les includes .h; msg; data accès; using namespace std_msgs; …; #include <std_msgs/Bool.h>; NodeHandle; Publisher ros::; Subsriber; String std_msgs::; string data; Char; char data; Bool; bool data; Int32; int32 data

http://wiki.ros.org/std_msgs

string data • Les messages standards : types de données de base
String std_msgs::
string data donnée structurée using namespace std_msgs; …

• Utilisation des messages

… msg.data = "hello world!";

Les messages standards

• Les librairies ros

Bool msg;
… msg.data = true;

std_msgs::Bool msg;

# Un publisher en C++

## Le master

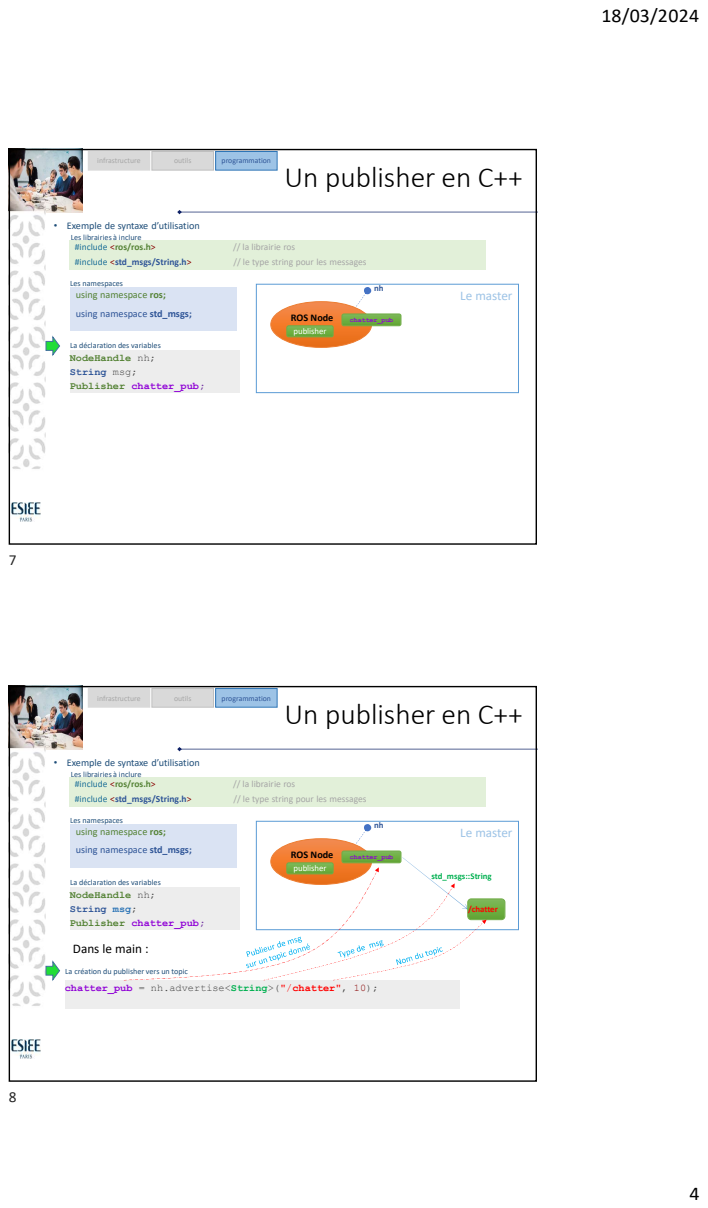
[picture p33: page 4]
infrastructure; outils; programmation #include <ros/ros.h>; // la librairie ros; #include <std_msgs/String.h>; // le type string pour les messages; Les namespaces; ROS Node; chatter_pub; publisher; Le master; std_msgs::String; /chatter

• Exemple de syntaxe d’utilisation
Les librairies à inclure using namespace ros; using namespace std_msgs;

La déclaration des variables
NodeHandle nh;
String msg;
Publisher chatter_pub;

Un publisher en C++

Les namespaces
nh chatter_pub = nh.advertise<String>("/chatter", 10);

Dans le main :

La création du publisher vers un topic

# Un publisher en C++

## Le master

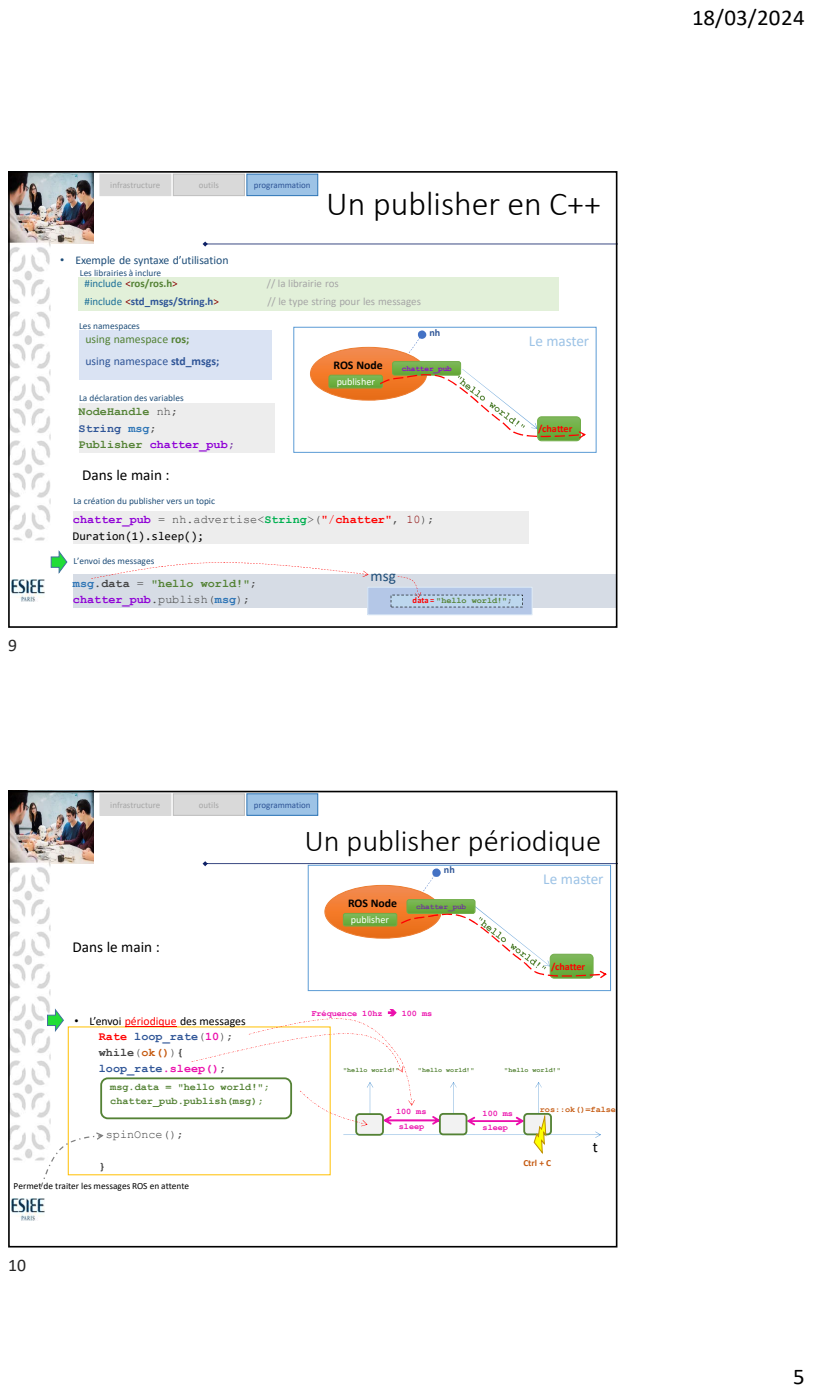
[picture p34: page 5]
infrastructure; outils; programmation #include <ros/ros.h>; // la librairie ros; #include <std_msgs/String.h>; // le type string pour les messages; ROS Node; chatter_pub; publisher; Duration(1).sleep();; /chatter; msg; spinOnce();; programmation; Le master; "hello world!"; sleep; Fréquence 10hz 100 ms; Ctrl + C

• Exemple de syntaxe d’utilisation
Les librairies à inclure using namespace ros; using namespace std_msgs;

Les namespaces
nh chatter_pub = nh.advertise<String>("/chatter", 10);

La déclaration des variables
NodeHandle nh;
String msg;
Publisher chatter_pub;

data = "hello world!"; Dans le main :

La création du publisher vers un topic

L’envoi des messages
msg.data = "hello world!";
chatter_pub.publish(msg);

Un publisher périodique

Dans le main :

• L’envoi périodique des messages
Rate loop_rate(10);
while(ok()){
loop_rate.sleep();

ros::ok()=false

Permet de traiter les messages ROS en attente

# Un subscriber en C++

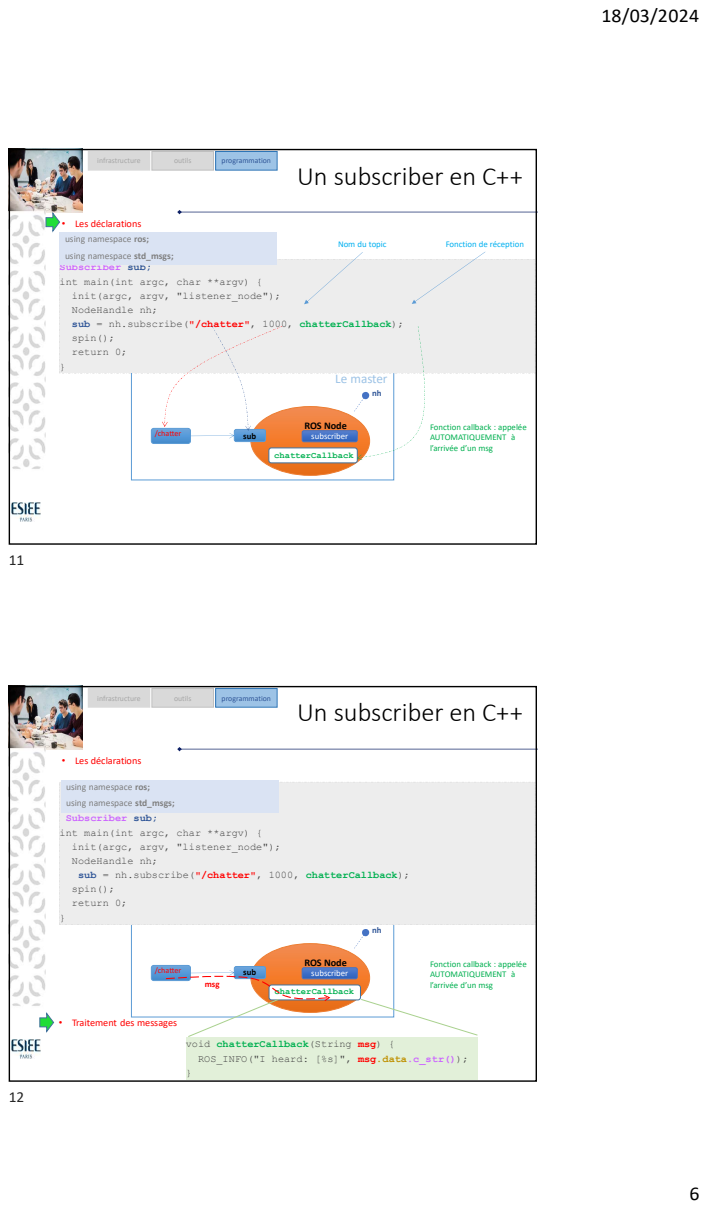
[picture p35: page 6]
ROS Node; /chatter; sub; chatterCallback; infrastructure; outils; programmation Subscriber sub;; Nom du topic; Fonction de réception; • Les déclarations; msg

• Les déclarations
using namespace ros; using namespace std_msgs;

int main(int argc, char **argv) {
init(argc, argv, "listener_node");
NodeHandle nh;
sub = nh.subscribe("/chatter", 1000, chatterCallback);
spin();
return 0;

subscriber Le master

Fonction callback : appelée
AUTOMATIQUEMENT à
l’arrivée d’un msg

Un subscriber en C++

• Traitement des messages

void chatterCallback(String msg) {
ROS_INFO("I heard: [%s]", msg.data.c_str());

## - Fréquence - Rate rate(10); // 10Hz

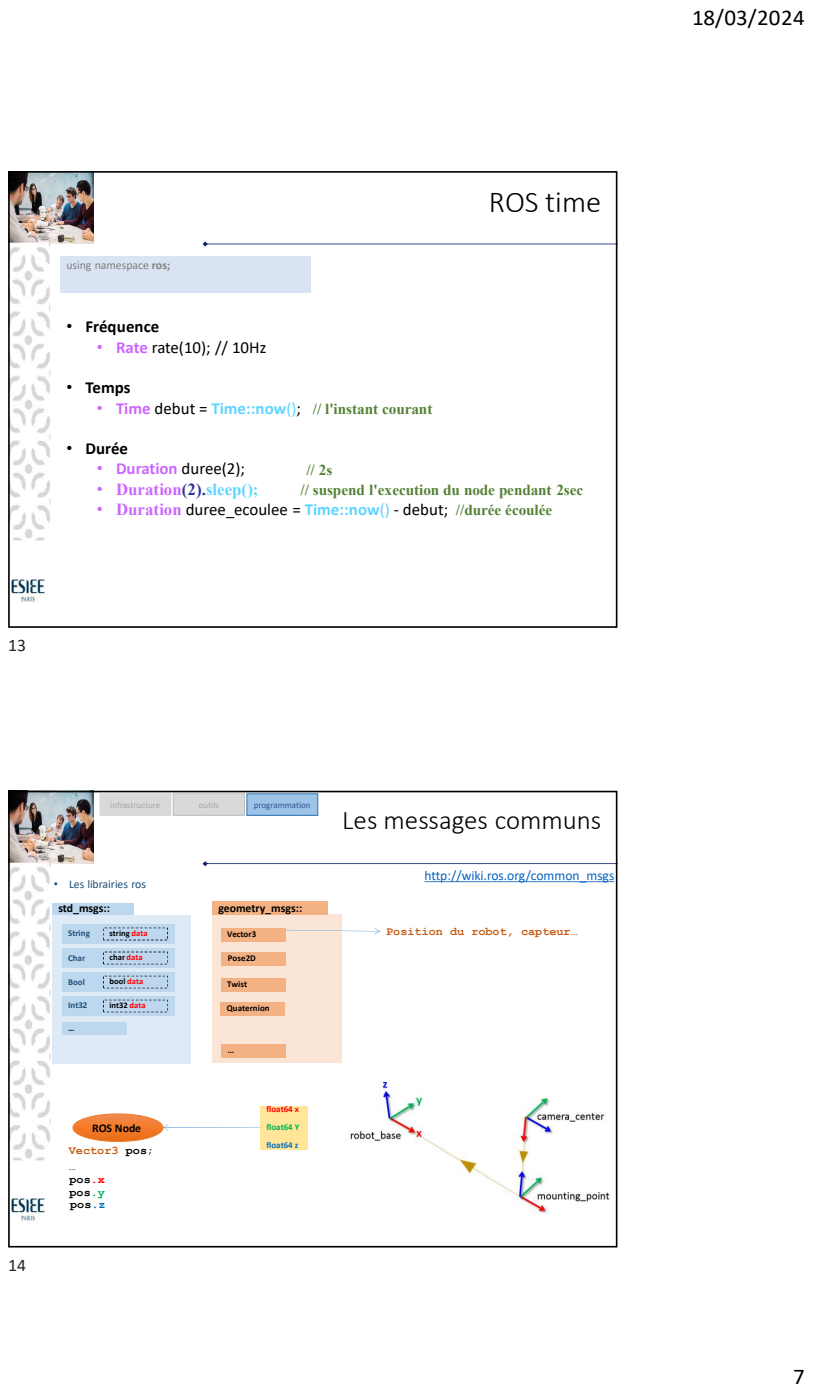
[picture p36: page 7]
• Duration duree(2);; // 2s • Duration(2).sleep();; // suspend l'execution du node pendant 2sec • Duration duree_ecoulee = Time::now() - debut; //durée écoulée; using namespace ros;; ROS time; infrastructure; outils; programmation • Les librairies ros; String std_msgs::; string data; Char; char data; Bool; bool data; Int32; int32 data; http://wiki.ros.org/common_msgs; Twist; Pose2D geometry_msgs::; Vector3; Quaternion Vector3 pos;; ROS Node; float64 x; float64 Y; float64 z pos.x; pos.z; pos.y

• Temps
• Time debut = Time::now(); // l'instant courant • Durée

Les messages communs

Position du robot, capteur…

# Les messages communs

### http://wiki.ros.org/common_msgs

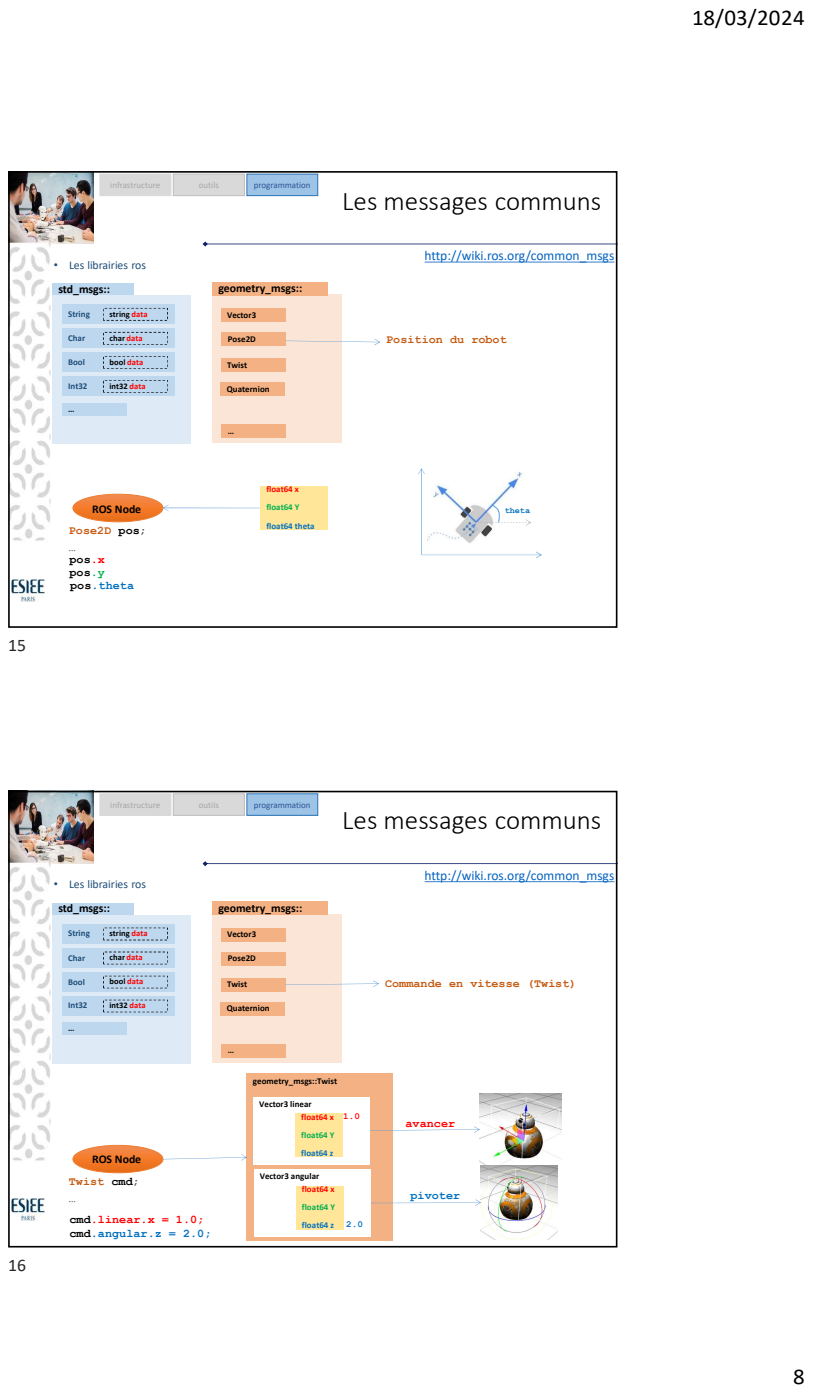
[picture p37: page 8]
infrastructure; outils; programmation • Les librairies ros; String std_msgs::; string data; Char; char data; Bool; bool data; Int32; int32 data; Twist; Pose2D geometry_msgs::; Vector3; Quaternion Pose2D pos;; ROS Node; float64 x; float64 Y; float64 theta pos.x; pos.theta; pos.y; theta; geometry_msgs::Twist; float64 z; float64 z Twist cmd; …; cmd.linear.x = 1.0; cmd.angular.z = 2.0;; Quaternion; avancer; pivoter

Position du robot

Les messages communs

http://wiki.ros.org/common_msgs

Commande en vitesse (Twist)

Vector3 linear

Vector3 angular

# Les messages communs

### http://wiki.ros.org/common_msgs

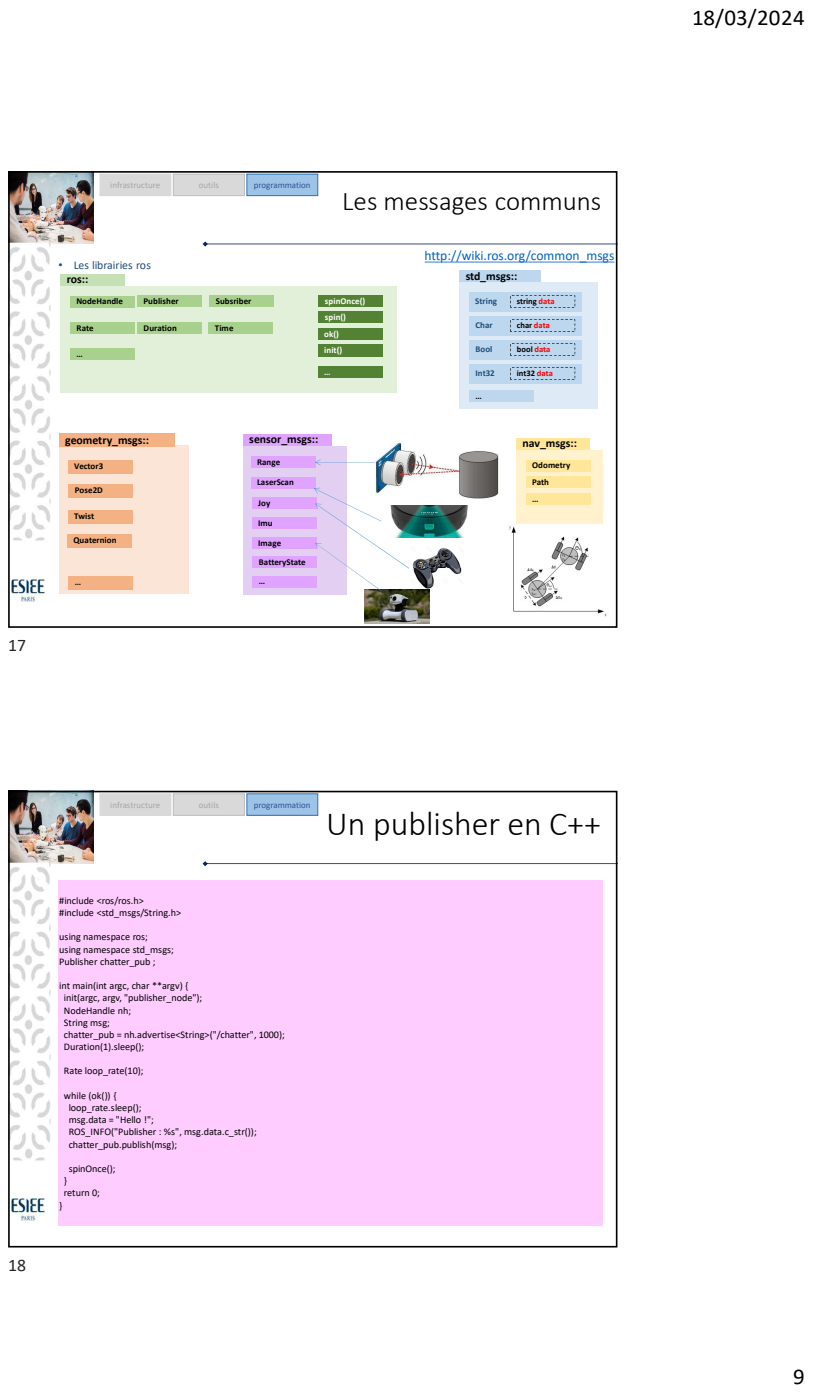
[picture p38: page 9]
infrastructure; outils; programmation • Les librairies ros; NodeHandle; Publisher ros::; Subsriber; String std_msgs::; Rate; spinOnce() spin(); string data; Char; char data; Bool; bool data; Int32; int32 data; Duration; Time; Odometry; Path nav_msgs::; … Joy; LaserScan sensor_msgs::; Imu; Image; BatteryState; Range; init(); Twist; Pose2D geometry_msgs::; Vector3; Quaternion; programmation; Rate loop_rate(10);; spinOnce();; } return 0;

Un publisher en C++

#include <ros/ros.h>
#include <std_msgs/String.h>

using namespace ros;
using namespace std_msgs;
Publisher chatter_pub ;

int main(int argc, char **argv) {
init(argc, argv, "publisher_node");
NodeHandle nh;
String msg;
chatter_pub = nh.advertise<String>("/chatter", 1000);
Duration(1).sleep();

while (ok()) {
loop_rate.sleep();
msg.data = "Hello !";
ROS_INFO("Publisher : %s", msg.data.c_str());
chatter_pub.publish(msg);

10

# Un subscriber en C++

infrastructure | outils | programmation #include <ros/ros.h>

### #include <std_msgs/String.h>

using namespace ros;
using namespace std_msgs;
Subscriber sub ;

### void chatterCallback(String msg) {

ROS_INFO("Chatter Listener : I heard: [%s]", msg.data.c_str()); }

### int main(int argc, char **argv) {

init(argc, argv, "listener_node");
NodeHandle nh;

sub = nh.subscribe("/chatter", 1000, chatterCallback);

spin();

return 0;
}

# ROSSERIAL - ARDUINO

19

20

# ROSSERIAL - publisher

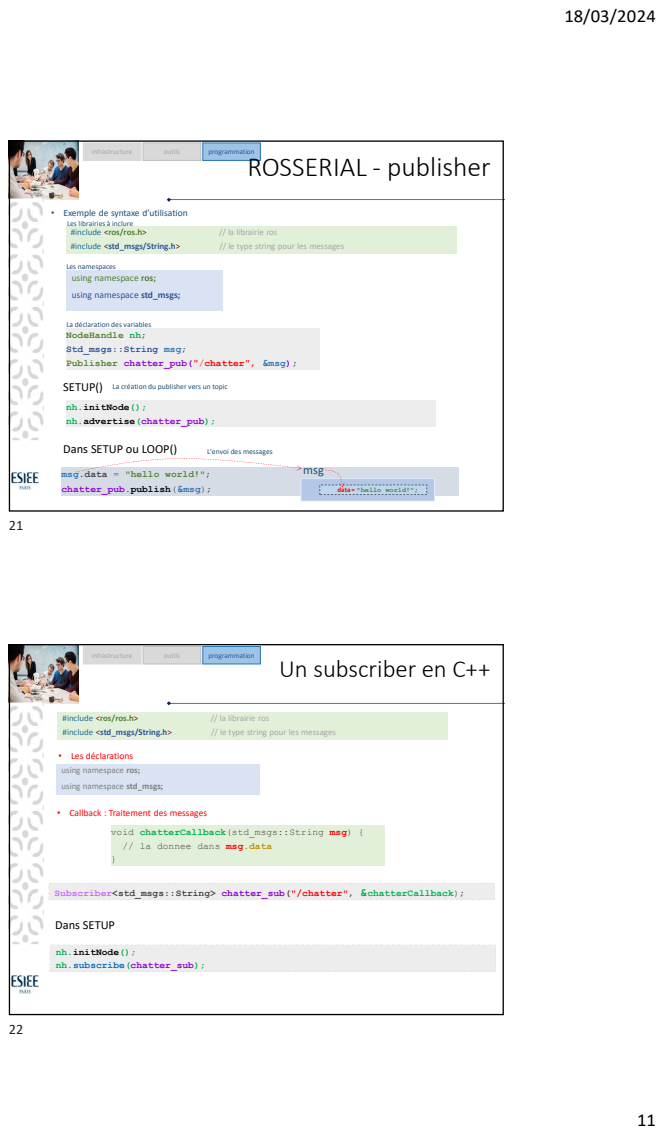
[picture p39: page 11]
infrastructure; outils; programmation #include <ros/ros.h>; // la librairie ros; #include <std_msgs/String.h>; // le type string pour les messages; Les namespaces; msg; programmation; nh.initNode(); nh.subscribe(chatter_sub);; Dans SETUP; #include <ros/ros.h>

• Exemple de syntaxe d’utilisation
Les librairies à inclure using namespace ros; using namespace std_msgs;

La déclaration des variables
NodeHandle nh;
Std_msgs::String msg;
Publisher chatter_pub("/chatter", &msg);

data = "hello world!"; SETUP()

La création du publisher vers un topic

nh.initNode();
nh.advertise(chatter_pub);
Dans SETUP ou LOOP()

L’envoi des messages

msg.data = "hello world!";
chatter_pub.publish(&msg);

Un subscriber en C++

• Les déclarations
using namespace ros; using namespace std_msgs;

• Callback : Traitement des messages

void chatterCallback(std_msgs::String msg) {
// la donnee dans msg.data

Subscriber<std_msgs::String> chatter_sub("/chatter", &chatterCallback);

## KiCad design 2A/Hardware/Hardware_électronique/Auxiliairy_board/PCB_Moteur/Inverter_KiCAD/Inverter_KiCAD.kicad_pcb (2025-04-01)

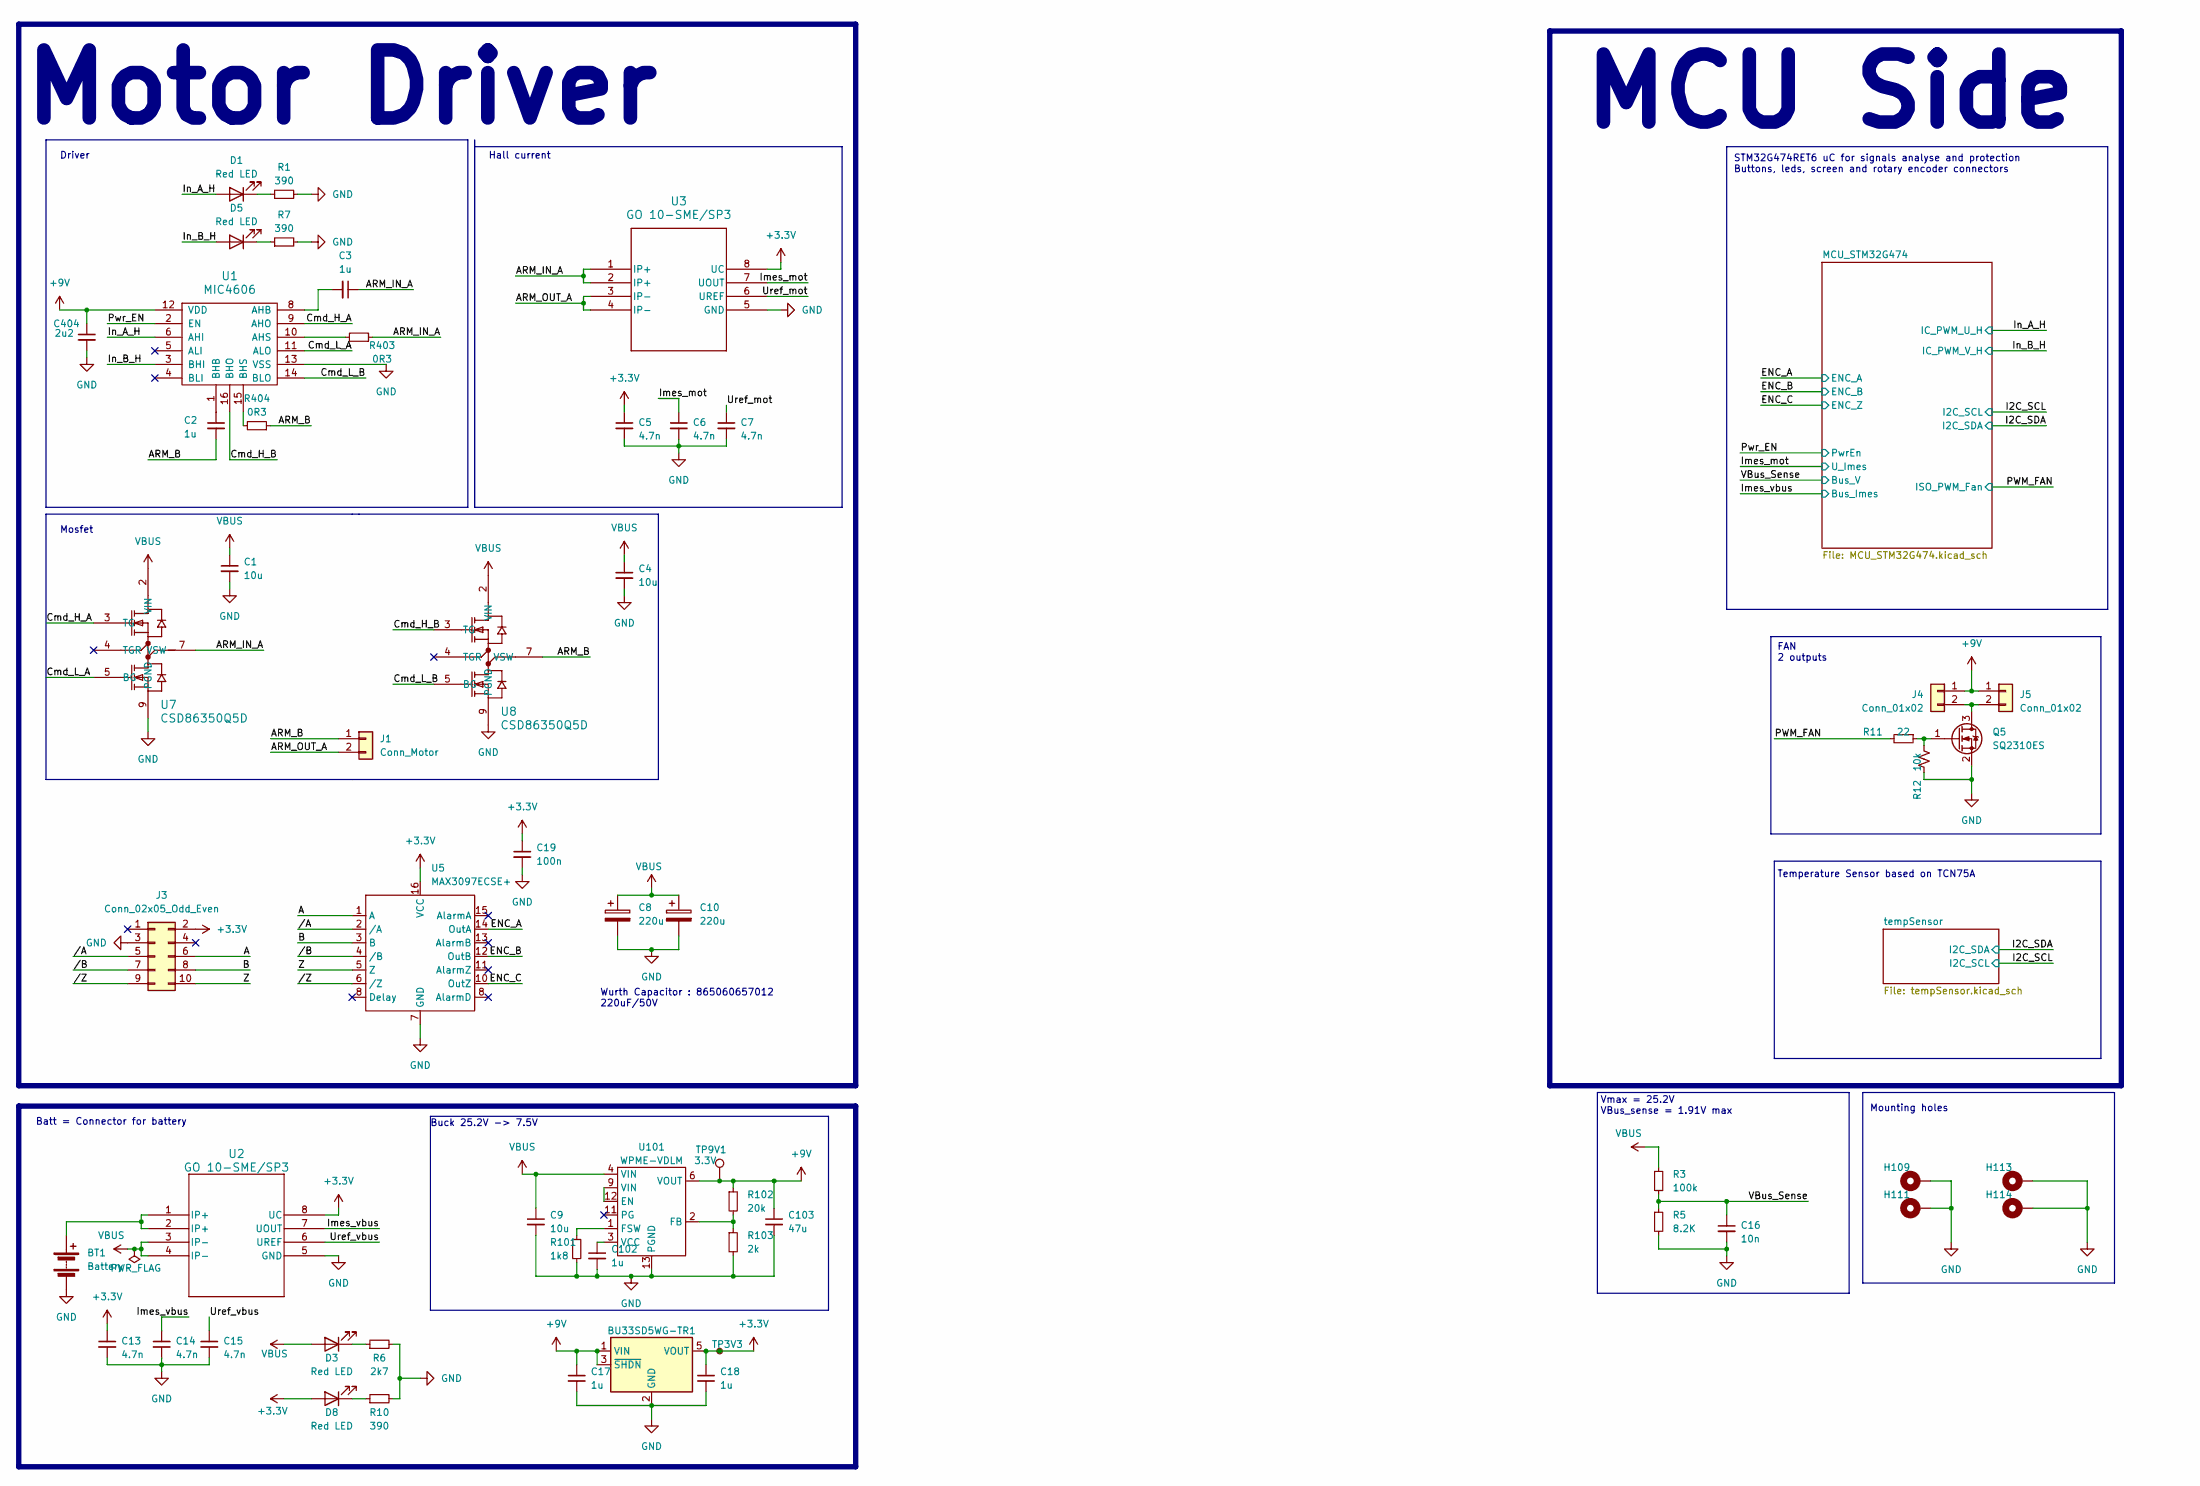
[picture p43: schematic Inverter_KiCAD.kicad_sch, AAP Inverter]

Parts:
BT1: Battery; AMASS_XT60-M_1x02_P7.20mm_Vertical
BU33SD5WG-TR1: LM1117DT-3.3; SOT-23-5
C1, C4, C9: 10u; C_2220_5750Metric
C2, C3: 1u; C_0805_2012Metric
C5, C6, C7, C13, C14, C15: 4.7n; C_0402_1005Metric
C8, C10: 220u; C_Elec_10x10.2
C16: 10n; C_0402_1005Metric
C17, C18: 1u; C_0603_1608Metric_Pad1.08x0.95mm_HandSolder
C19: 100n; C_0402_1005Metric
C102: 1u; C_0603_1608Metric
C103: 47u; C_0805_2012Metric
C404: 2u2; C_0603_1608Metric
D1, D3, D5, D8: Red LED; LED_0603_1608Metric
H109, H111, H113, H114: MountingHole_Pad; MountingHole_3.2mm_M3_Pad_Via
J1: Conn_Motor; AMASS_XT30UPB-F_1x02_P5.0mm_Vertical
J3: Conn_02x05_Odd_Even; PinHeader_2x05_P1.27mm_Vertical_SMD
J4, J5: Conn_01x02; JST_XH_B2B-XH-A_1x02_P2.50mm_Vertical
Q5: SQ2310ES; SOT-23
R1, R7, R10: 390; R_0402_1005Metric
R3: 100k; R_0402_1005Metric
R5: 8.2K; R_0402_1005Metric
R6: 2k7; R_0402_1005Metric
R11: 22; R_0402_1005Metric
R12: 10k; R_0402_1005Metric
R101: 1k8; R_0402_1005Metric
R102: 20k; R_0402_1005Metric
R103: 2k; R_0402_1005Metric
R403, R404: 0R3; R_1210_3225Metric
TP3V3: TestPoint_Small; TestPoint_Pad_D1.0mm
TP9V1: 3.3V; TestPoint_Pad_D1.0mm
U1: MIC4606; TSSOP-16_4.4x5mm_P0.65mm
U2, U3: GO 10-SME/SP3; SOIC8-GO-SME&slash_SP3_LEM
U5: MAX3097ECSE+; SOIC-16_3.9x9.9mm_P1.27mm
U7, U8: CSD86350Q5D; DQY0008A
U101: WPME-VDLM; MPN 171013801

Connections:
+3.3V: BU33SD5WG-TR1.5 (VOUT), C5.1, C13.1, C18.1, C19.1, D8.2 (A), J3.2, TP3V3.1, U2.8 (UC), U3.8 (UC), U5.16 (VCC); also elsewhere on the board
+9V: BU33SD5WG-TR1.1 (VIN), BU33SD5WG-TR1.3 (~SHDN), C17.1, C103.1, C404.1, J4.1, J5.1, R102.1, TP9V1.1, U1.12 (VDD), U101.6 (VOUT), U101.7 (VOUT)
/A: J3.6, U5.1 (A)
/ARM_B: C2.2, J1.1, R404.1, U8.6 (VSW), U8.7 (VSW), U8.8 (VSW)
/ARM_IN_A: C3.1, R403.1, U3.1 (IP+), U3.2 (IP+), U7.6 (VSW), U7.7 (VSW), U7.8 (VSW)
/ARM_OUT_A: J1.2, U3.3 (IP-), U3.4 (IP-)
/B: J3.8, U5.3 (B)
/Cmd_H_A: U1.9 (AHO), U7.3 (TG)
/Cmd_H_B: U1.16 (BHO), U8.3 (TG)
/Cmd_L_A: U1.11 (ALO), U7.5 (BG)
/Cmd_L_B: U1.14 (BLO), U8.5 (BG)
/ENC_A: U5.14 (OutA); also elsewhere on the board
/ENC_B: U5.12 (OutB); also elsewhere on the board
/ENC_C: U5.10 (OutZ); also elsewhere on the board
/Imes_mot: C6.1, U3.7 (UOUT); also elsewhere on the board
/Imes_vbus: C14.1, U2.7 (UOUT); also elsewhere on the board
/In_A_H: D1.2 (A), U1.6 (AHI); also elsewhere on the board
/In_B_H: D5.2 (A), U1.3 (BHI); also elsewhere on the board
/PWM_FAN: R11.2; also elsewhere on the board
/Pwr_EN: U1.2 (EN); also elsewhere on the board
/Uref_mot: C7.1, U3.6 (UREF)
/Uref_vbus: C15.1, U2.6 (UREF)
/VBus_Sense: C16.1, R3.2, R5.1; also elsewhere on the board
/Z: J3.10, U5.5 (Z)
//A: J3.5, U5.2 (/A)
//B: J3.7, U5.4 (/B)
//Z: J3.9, U5.6 (/Z)
GND: BT1.1 (-), BU33SD5WG-TR1.2 (GND), C1.2, C4.2, C5.2, C6.2, C7.2, C8.2, C9.2, C10.2, C13.2, C14.2, C15.2, C16.2, C17.2, C18.2, C19.2, C102.2, C103.2, C404.2, H109.1, H111.1, H113.1, H114.1, J3.3, Q5.2 (S), R1.2, R5.2, R6.2, R7.2, R10.2, R12.2, R101.2, R103.2, U1.13 (VSS), U2.5 (GND), U3.5 (GND), U5.7 (GND), U7.9 (PGND), U8.9 (PGND), U101.10 (AGND), U101.13 (PGND); also elsewhere on the board
unnamed: BT1.2 (+), U2.1 (IP+), U2.2 (IP+)
unnamed: D1.1 (K), R1.1
unnamed: D3.1 (K), R6.1
unnamed: D5.1 (K), R7.1
unnamed: D8.1 (K), R10.1
unnamed: J4.2, J5.2, Q5.3 (D)
unnamed: Q5.1 (G), R11.1, R12.1
unnamed: C3.2, U1.8 (AHB)
unnamed: R403.2, U1.10 (AHS)
unnamed: C2.1, U1.1 (BHB)
unnamed: R404.2, U1.15 (BHS)
unnamed: U101.9 (VIN), U101.12 (EN)
unnamed: R102.2, R103.1, U101.2 (FB)
unnamed: R101.1, U101.1 (FSW)
unnamed: C102.1, U101.3 (VCC)
VBUS: C1.1, C4.1, C8.1, C9.1, C10.1, D3.2 (A), R3.1, U2.3 (IP-), U2.4 (IP-), U7.1 (VIN), U7.2 (VIN), U8.1 (VIN), U8.2 (VIN), U101.4 (VIN), U101.5 (VIN)

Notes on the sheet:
Temperature Sensor based on TCN75A
STM32G474RET6 uC for signals analyse and protection Buttons, leds, screen and rotary encoder connectors
Mounting holes
Hall current
Mosfet
Vmax = 25.2V VBus_sense = 1.91V max
Wurth Capacitor : 865060657012 220uF/50V
Batt = Connector for battery
Driver
MCU Side
FAN 2 outputs
Buck 25.2V -> 7.5V
Motor Driver

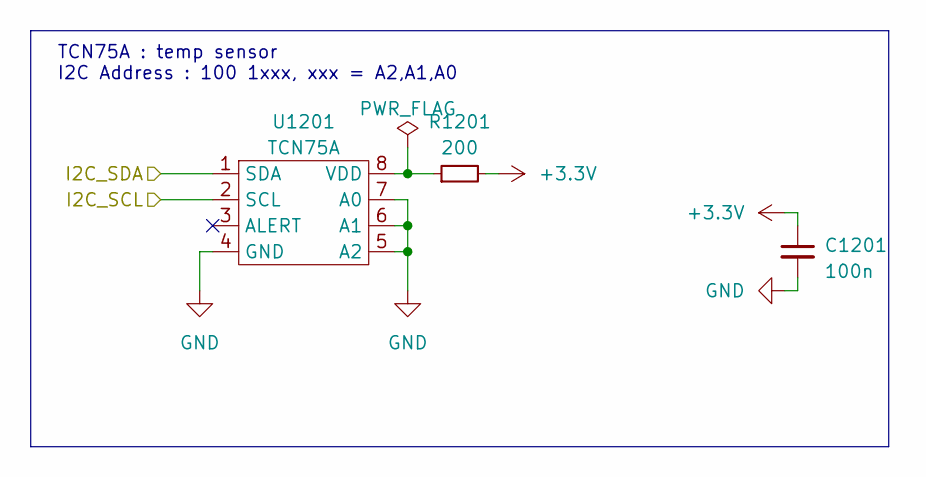
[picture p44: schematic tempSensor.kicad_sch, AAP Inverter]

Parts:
C1201: 100n; C_0402_1005Metric
R1201: 200; R_0402_1005Metric
U1201: TCN75A; SOIC-8_3.9x4.9mm_P1.27mm

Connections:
+3.3V: C1201.1, R1201.2; also elsewhere on the board
/I2C_SCL: U1201.2 (SCL); also elsewhere on the board
/I2C_SDA: U1201.1 (SDA); also elsewhere on the board
GND: C1201.2, U1201.4 (GND), U1201.5 (A2), U1201.6 (A1), U1201.7 (A0); also elsewhere on the board
unnamed: R1201.1, U1201.8 (VDD)

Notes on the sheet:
TCN75A : temp sensor I2C Address : 100 1xxx, xxx = A2,A1,A0

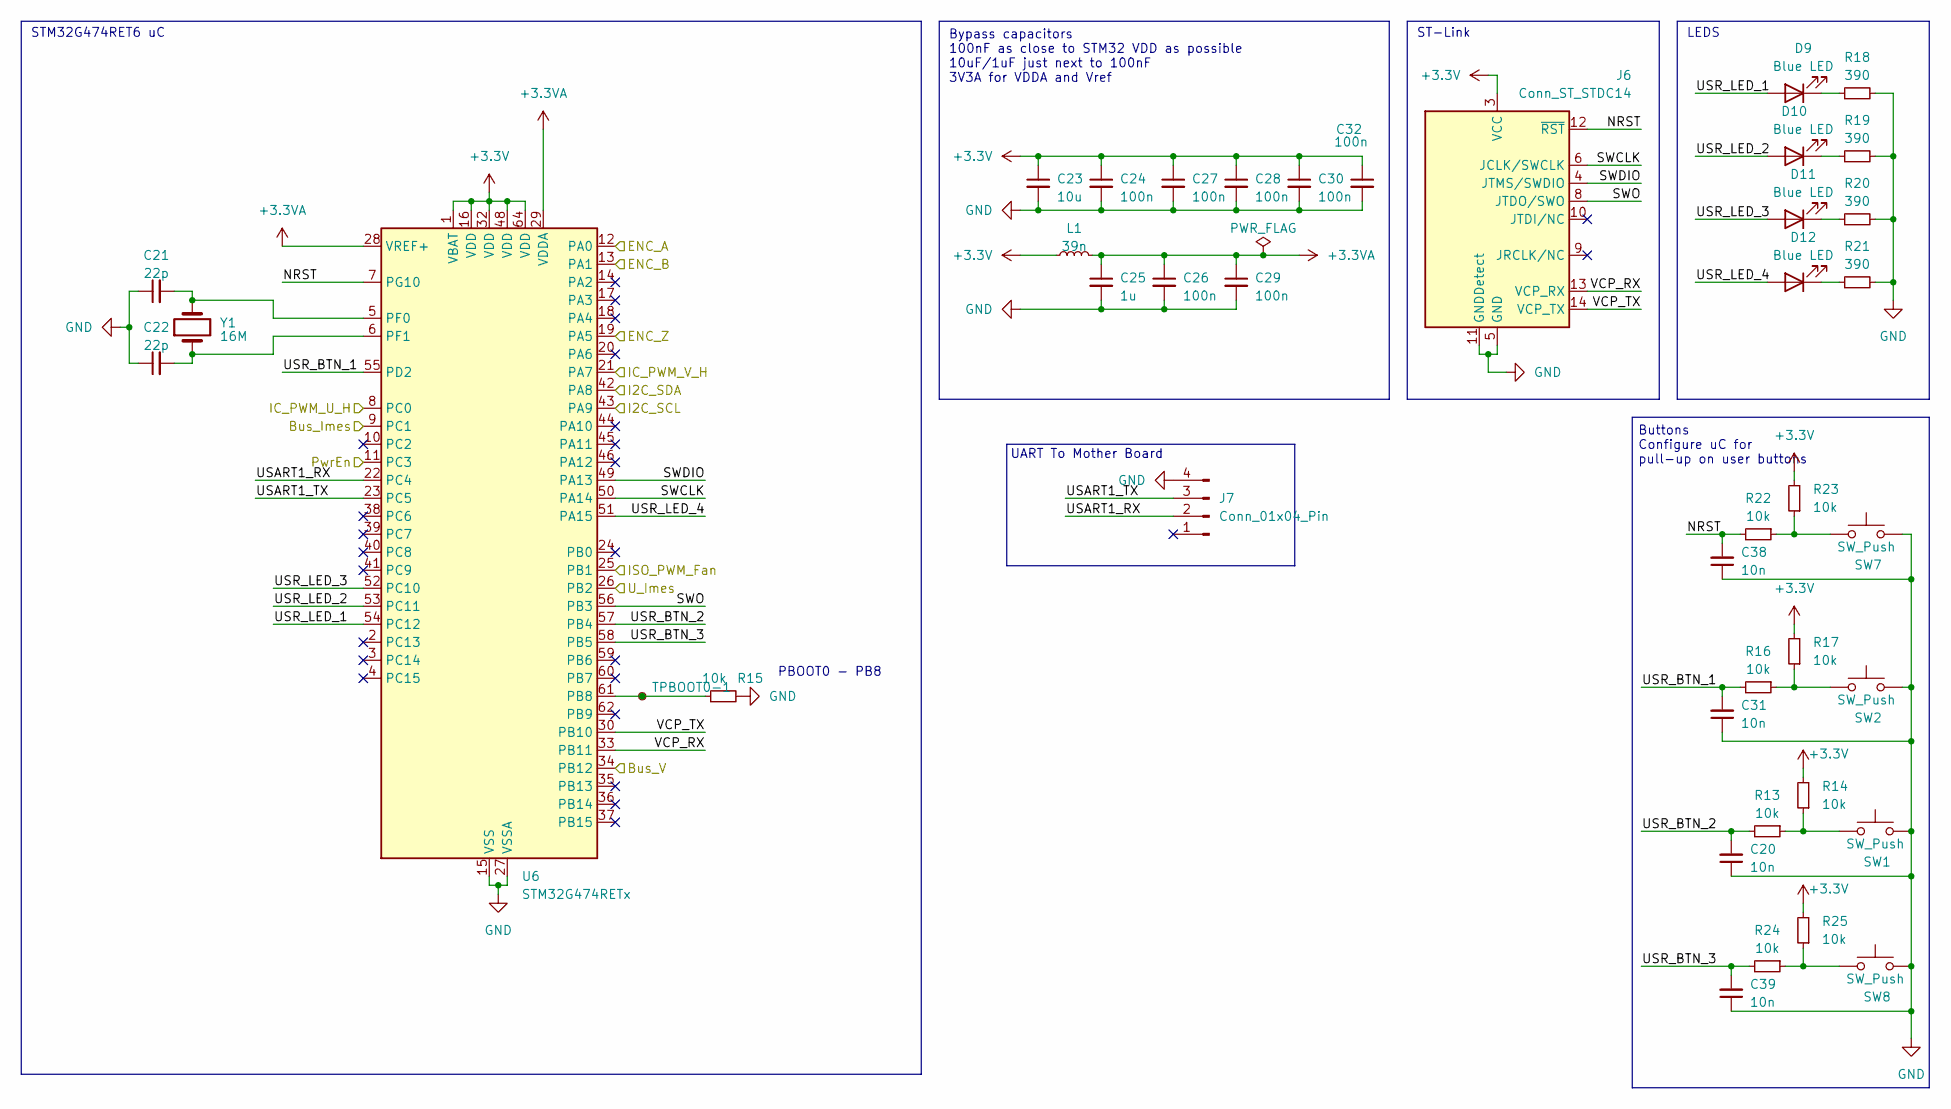
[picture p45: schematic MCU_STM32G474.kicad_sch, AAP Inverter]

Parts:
C20, C31, C38, C39: 10n; C_0402_1005Metric
C21, C22: 22p; C_0402_1005Metric
C23: 10u; C_0603_1608Metric_Pad1.08x0.95mm_HandSolder
C24, C26, C27, C28, C29, C30, C32: 100n; C_0402_1005Metric
C25: 1u; C_0603_1608Metric_Pad1.08x0.95mm_HandSolder
D9, D10, D11, D12: Blue LED; LED_0603_1608Metric
J6: Conn_ST_STDC14; PinHeader_2x07_P1.27mm_Vertical_SMD
J7: Conn_01x04_Pin; JST_XH_B4B-XH-A_1x04_P2.50mm_Vertical
L1: 39n; L_0603_1608Metric
R13, R14, R15, R16, R17, R22, R23, R24, R25: 10k; R_0402_1005Metric
R18, R19, R20, R21: 390; R_0402_1005Metric
SW1, SW2, SW7, SW8: SW_Push; 435451019820
TPBOOT0-1: TestPoint_Small; TestPoint_Pad_D1.0mm
U6: STM32G474RETx; LQFP-64_10x10mm_P0.5mm
Y1: 16M; ABLS-7.3728MHZ-CL-RESR-A-1-G-F

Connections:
+3.3V: C23.1, C24.1, C27.1, C28.1, C30.1, C32.1, J6.3 (VCC), L1.1, R14.2, R17.2, R23.2, R25.2, U6.1 (VBAT), U6.16 (VDD), U6.32 (VDD), U6.48 (VDD), U6.64 (VDD); also elsewhere on the board
+3.3VA: C25.1, C26.1, C29.1, L1.2, U6.28 (VREF+), U6.29 (VDDA)
/ENC_A: U6.12 (PA0); also elsewhere on the board
/ENC_B: U6.13 (PA1); also elsewhere on the board
/ENC_C: U6.19 (PA5); also elsewhere on the board
/I2C_SCL: U6.43 (PA9); also elsewhere on the board
/I2C_SDA: U6.42 (PA8); also elsewhere on the board
/Imes_mot: U6.26 (PB2); also elsewhere on the board
/Imes_vbus: U6.9 (PC1); also elsewhere on the board
/In_A_H: U6.8 (PC0); also elsewhere on the board
/In_B_H: U6.21 (PA7); also elsewhere on the board
/MCU_STM32G474/NRST: C38.2, J6.12 (~RST), R22.2, U6.7 (PG10)
/MCU_STM32G474/SWCLK: J6.6 (JCLK/SWCLK), U6.50 (PA14)
/MCU_STM32G474/SWDIO: J6.4 (JTMS/SWDIO), U6.49 (PA13)
/MCU_STM32G474/SWO: J6.8 (JTDO/SWO), U6.56 (PB3)
/MCU_STM32G474/USART1_RX: J7.2, U6.22 (PC4)
/MCU_STM32G474/USART1_TX: J7.3, U6.23 (PC5)
/MCU_STM32G474/USR_BTN_1: C31.2, R16.2, U6.55 (PD2)
/MCU_STM32G474/USR_BTN_2: C20.2, R13.2, U6.57 (PB4)
/MCU_STM32G474/USR_BTN_3: C39.2, R24.2, U6.58 (PB5)
/MCU_STM32G474/USR_LED_1: D9.2 (A), U6.54 (PC12)
/MCU_STM32G474/USR_LED_2: D10.2 (A), U6.53 (PC11)
/MCU_STM32G474/USR_LED_3: D11.2 (A), U6.52 (PC10)
/MCU_STM32G474/USR_LED_4: D12.2 (A), U6.51 (PA15)
/MCU_STM32G474/VCP_RX: J6.13 (VCP_RX), U6.33 (PB11)
/MCU_STM32G474/VCP_TX: J6.14 (VCP_TX), U6.30 (PB10)
/PWM_FAN: U6.25 (PB1); also elsewhere on the board
/Pwr_EN: U6.11 (PC3); also elsewhere on the board
/VBus_Sense: U6.34 (PB12); also elsewhere on the board
GND: C20.1, C21.1, C22.1, C23.2, C24.2, C25.2, C26.2, C27.2, C28.2, C29.2, C30.2, C31.1, C32.2, C38.1, C39.1, J6.5 (GND), J6.7 (GND), J6.11 (GNDDetect), J7.4, R15.2, R18.2, R19.2, R20.2, R21.2, SW1.2, SW2.2, SW7.2, SW8.2, U6.15 (VSS), U6.27 (VSSA), U6.31 (VSS), U6.47 (VSS), U6.63 (VSS); also elsewhere on the board
unnamed: D9.1 (K), R18.1
unnamed: D10.1 (K), R19.1
unnamed: D11.1 (K), R20.1
unnamed: D12.1 (K), R21.1
unnamed: R13.1, R14.1, SW1.1
unnamed: R16.1, R17.1, SW2.1
unnamed: R22.1, R23.1, SW7.1
unnamed: R24.1, R25.1, SW8.1
unnamed: R15.1, TPBOOT0-1.1, U6.61 (PB8)
unnamed: C21.2, U6.5 (PF0), Y1.2
unnamed: C22.2, U6.6 (PF1), Y1.1

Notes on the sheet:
ST-Link
Bypass capacitors 100nF as close to STM32 VDD as possible 10uF/1uF just next to 100nF 3V3A for VDDA and Vref
Buttons Configure uC for pull-up on user buttons
UART To Mother Board
PBOOT0 - PB8
STM32G474RET6 uC
LEDS

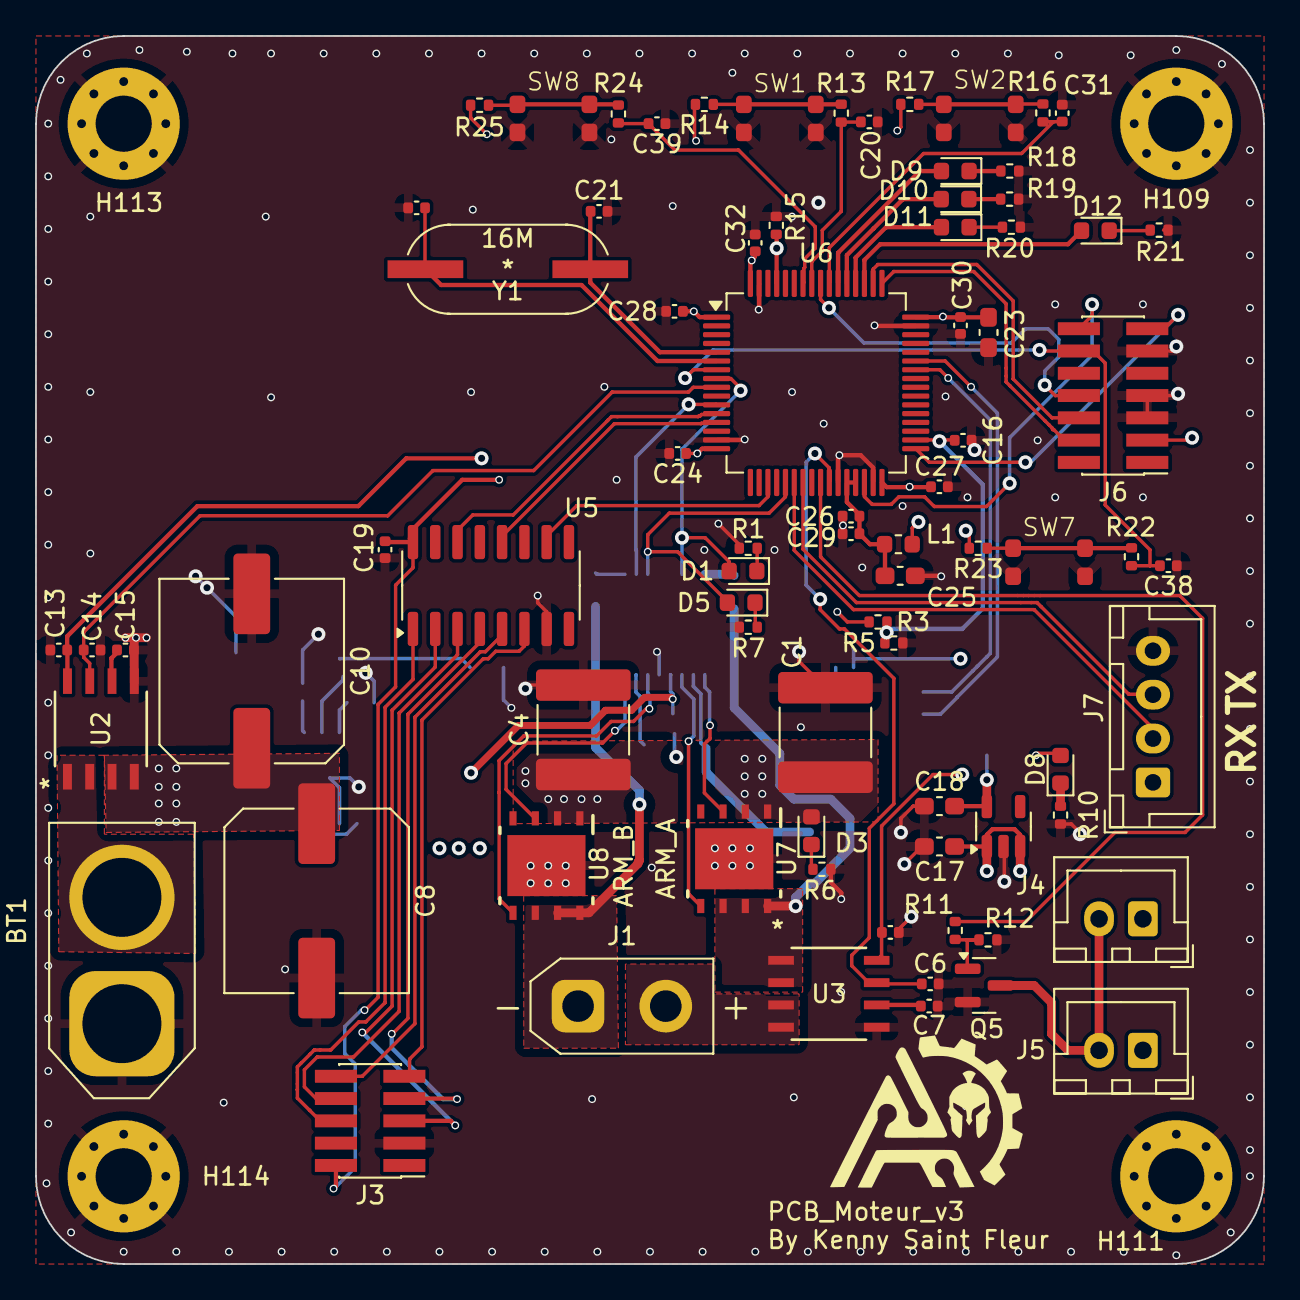
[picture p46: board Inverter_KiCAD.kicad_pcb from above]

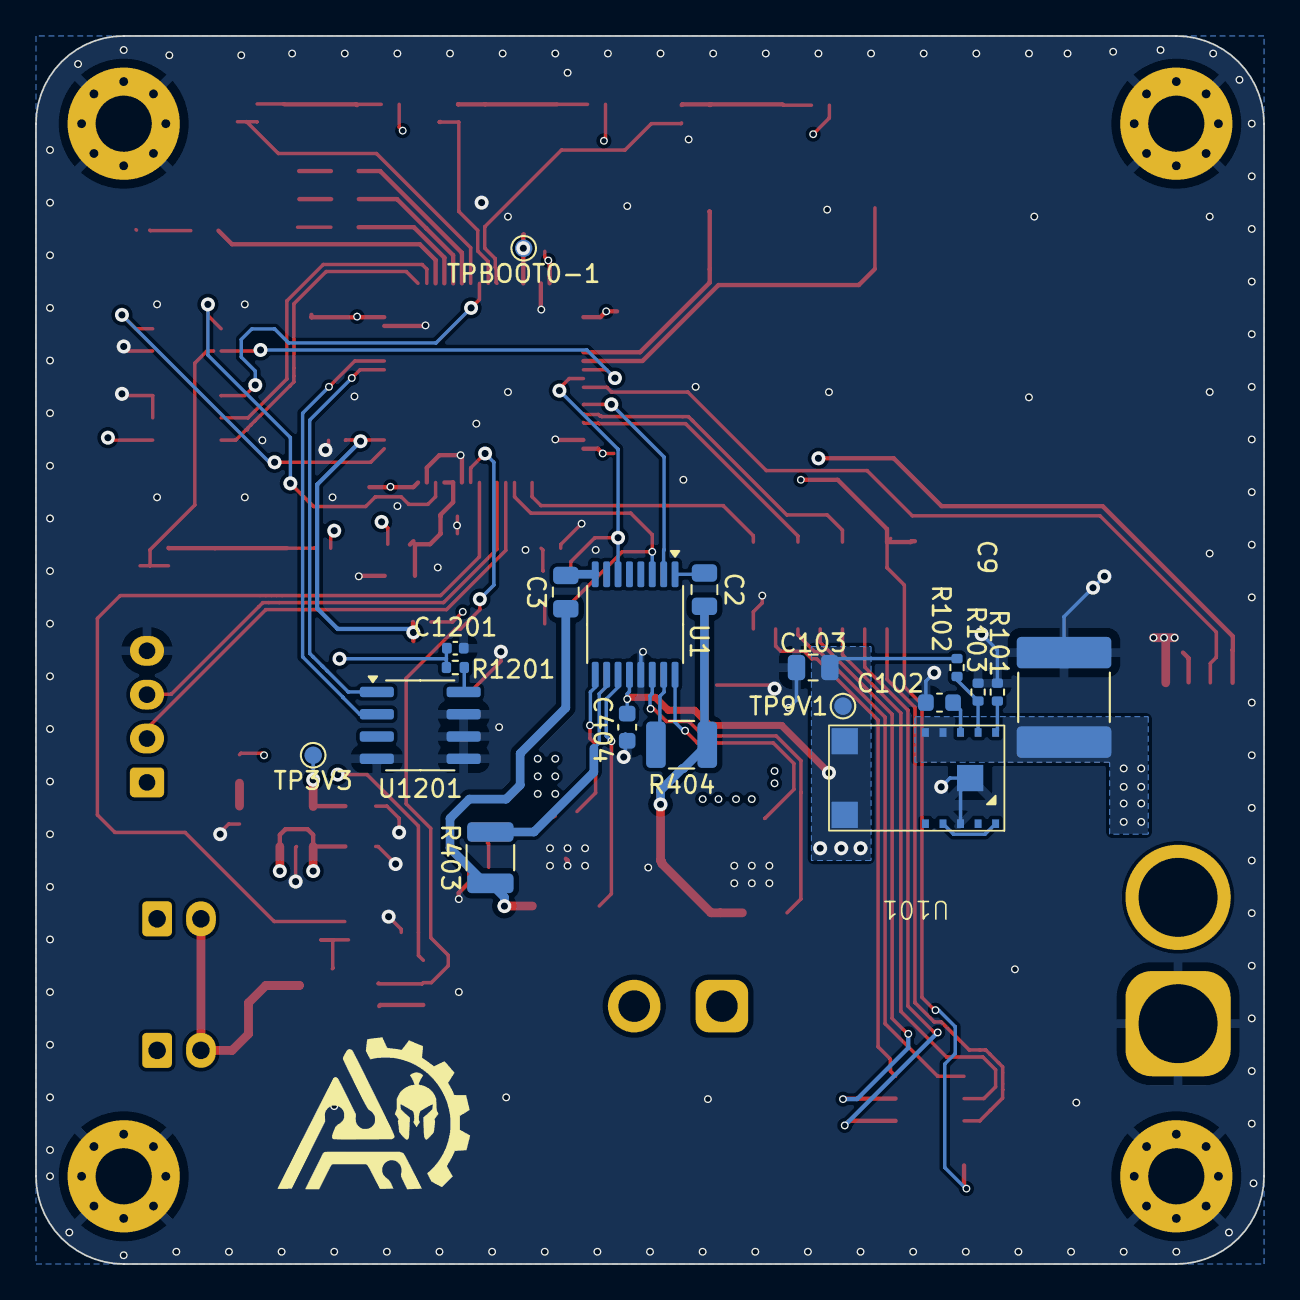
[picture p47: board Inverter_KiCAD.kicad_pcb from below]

Board: 4 copper layers, 70.0 x 70.0 mm, 102 parts (19 on the bottom side), 74 nets.

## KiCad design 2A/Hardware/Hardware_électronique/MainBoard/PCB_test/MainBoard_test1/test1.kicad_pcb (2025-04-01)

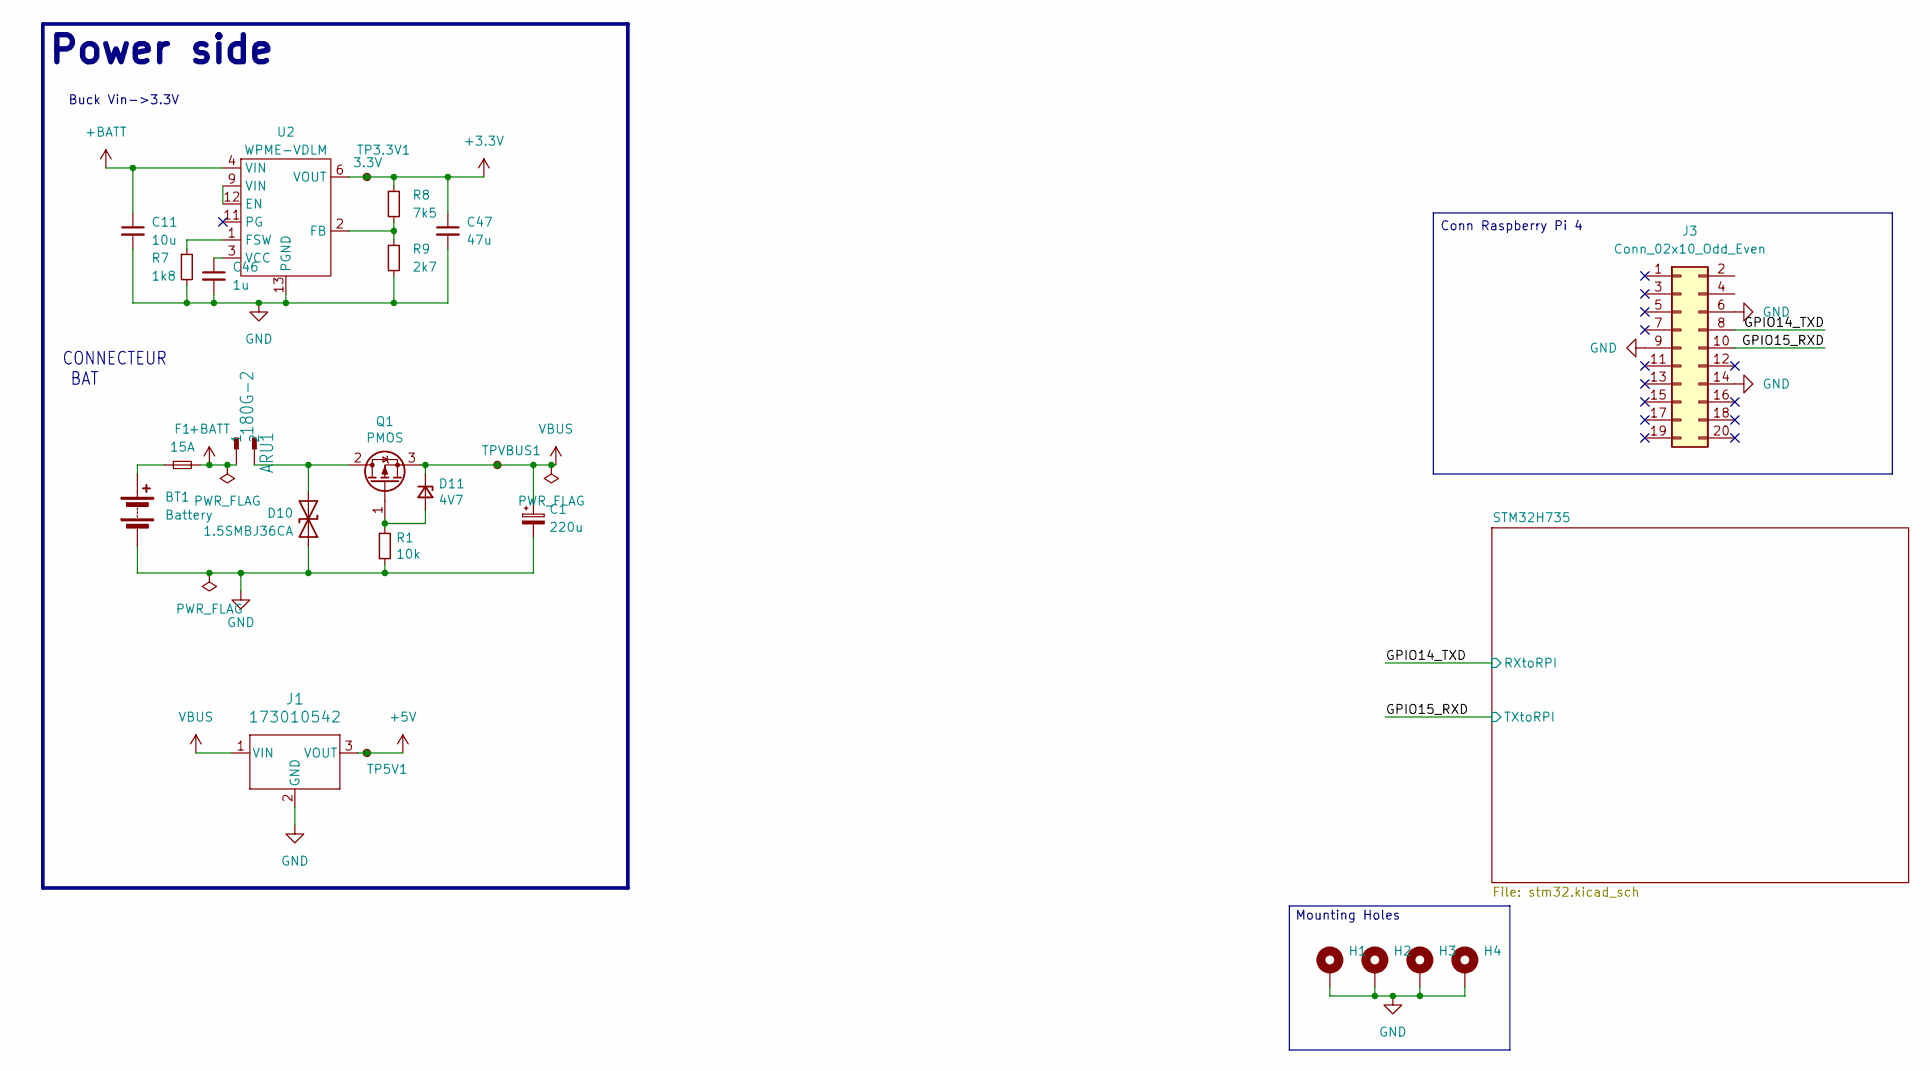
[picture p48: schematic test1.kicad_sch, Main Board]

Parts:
ARU1: 180G-2
BT1: Battery; AMASS_XT60-F_1x02_P7.20mm_Vertical
C1: 220u; CP_Elec_10x10.5
C11: 10u; C_0805_2012Metric
C46: 1u; C_0603_1608Metric
C47: 47u; C_0805_2012Metric
D10: 1.5SMBJ36CA; D_SMB; Mouser Part Number 652-1.5SMBJ36CA-H
D11: 4V7; D_0603_1608Metric; Mouser Part Number 771-BZX84J-C4V7115
F1: 15A; Fuse_1206_3216Metric
H1, H2, H3, H4: MountingHole_Pad; MountingHole_2.7mm_M2.5_DIN965_Pad
J1: 173010542; PinHeader_1x03_P2.54mm_Vertical; MPN 173010542
J3: Conn_02x10_Odd_Even; PinSocket_2x10_P2.54mm_Vertical
Q1: PMOS; MOS_WDFN8; Mouser Part Number 863-NTTFS015P03P8ZWG
R1: 10k; R_0402_1005Metric
R7: 1k8; R_0402_1005Metric
R8: 7k5; R_0402_1005Metric
R9: 2k7; R_0402_1005Metric
TP3.3V1, TP5V1: 3.3V; TestPoint_Pad_D1.0mm
TPVBUS1: 3.3V; TestPoint_Pad_D1.0mm
U2: WPME-VDLM; MPN 171013801

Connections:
+3.3V: C47.1, R8.1, TP3.3V1.1, U2.6 (VOUT), U2.7 (VOUT); also elsewhere on the board
+5V: J1.3 (VOUT), TP5V1.1; also elsewhere on the board
+BATT: ARU1.1, C11.1, F1.2, U2.4 (VIN), U2.5 (VIN)
/GPIO14_TXD: J3.8; also elsewhere on the board
/GPIO15_RXD: J3.10; also elsewhere on the board
GND: BT1.2 (-), C1.2, C11.2, C46.2, C47.2, D10.1 (A1), H1.1, H2.1, H3.1, H4.1, J1.2 (GND), J3.6, J3.9, J3.14, R1.2, R7.2, R9.2, U2.10 (AGND), U2.13 (PGND); also elsewhere on the board
unnamed: BT1.1 (+), F1.1
unnamed: ARU1.2, D10.2 (A2), Q1.2 (D)
unnamed: D11.2 (A), Q1.1 (G), R1.1
unnamed: U2.9 (VIN), U2.12 (EN)
unnamed: R8.2, R9.1, U2.2 (FB)
unnamed: R7.1, U2.1 (FSW)
unnamed: C46.1, U2.3 (VCC)
VBUS: C1.1, D11.1 (K), J1.1 (VIN), Q1.3 (S), TPVBUS1.1; also elsewhere on the board

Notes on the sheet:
Conn Raspberry Pi 4
CONNECTEUR BAT
Buck Vin->3.3V
Power side
Mounting Holes

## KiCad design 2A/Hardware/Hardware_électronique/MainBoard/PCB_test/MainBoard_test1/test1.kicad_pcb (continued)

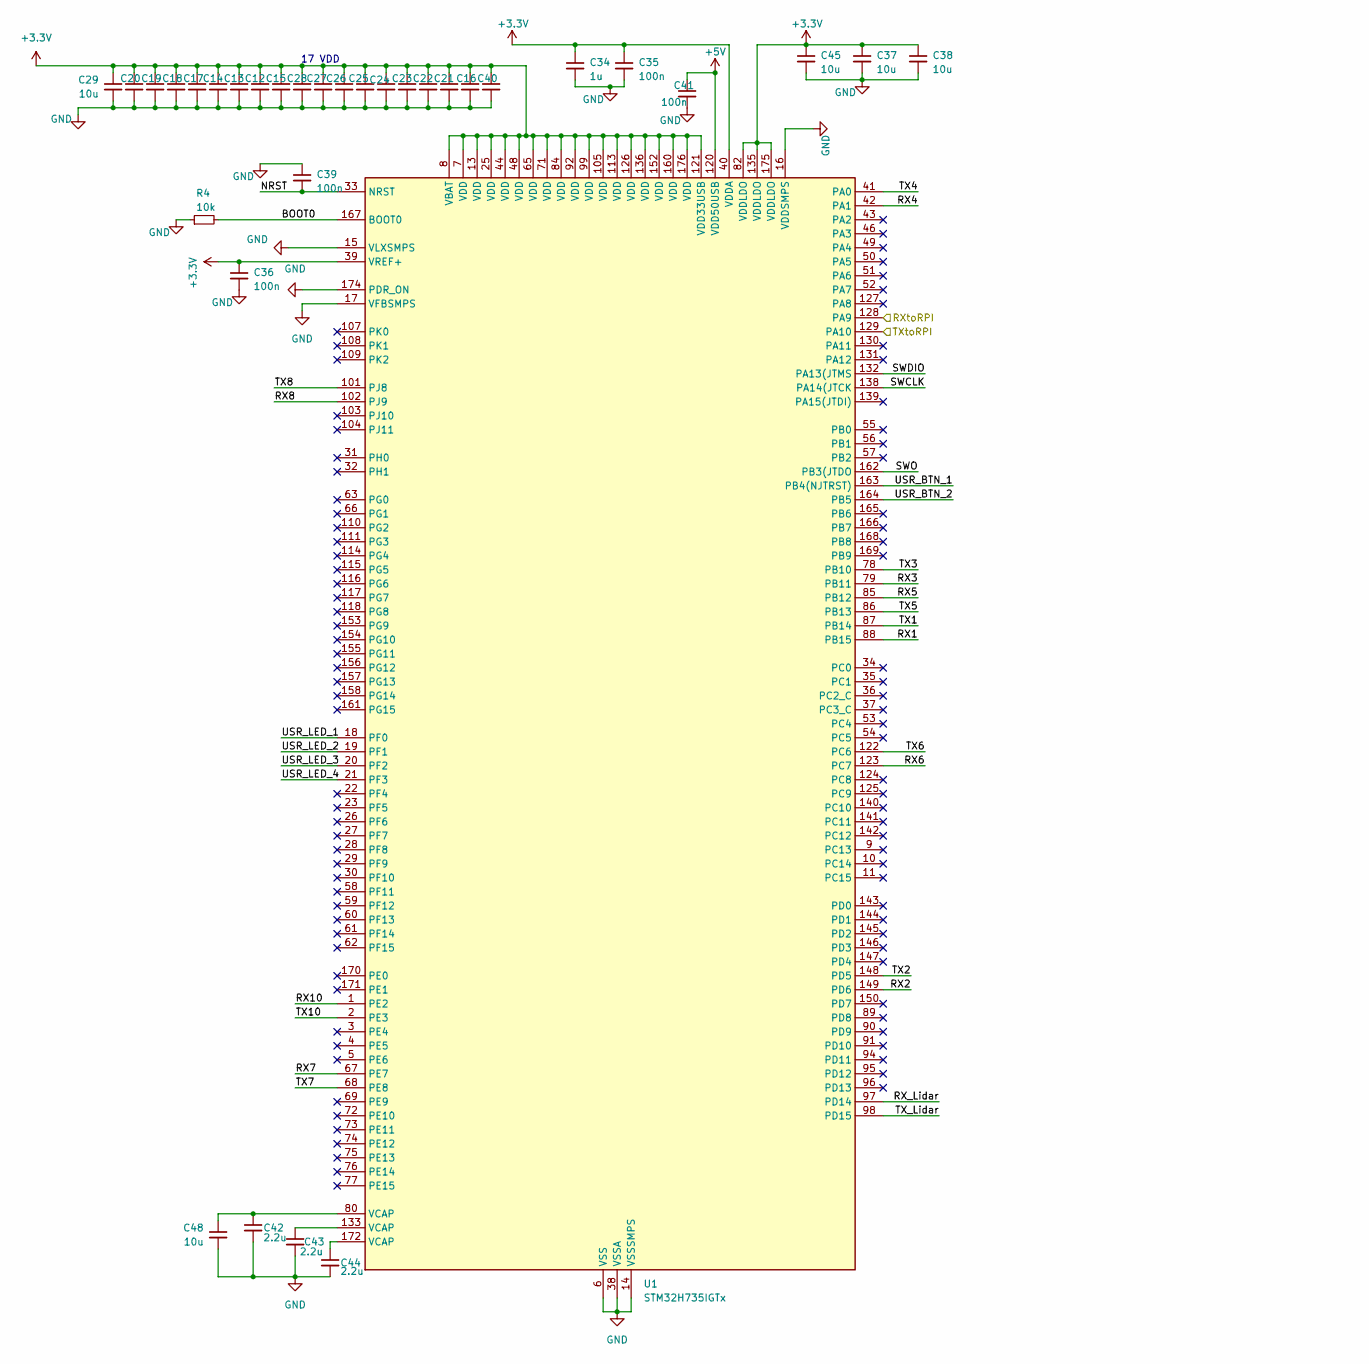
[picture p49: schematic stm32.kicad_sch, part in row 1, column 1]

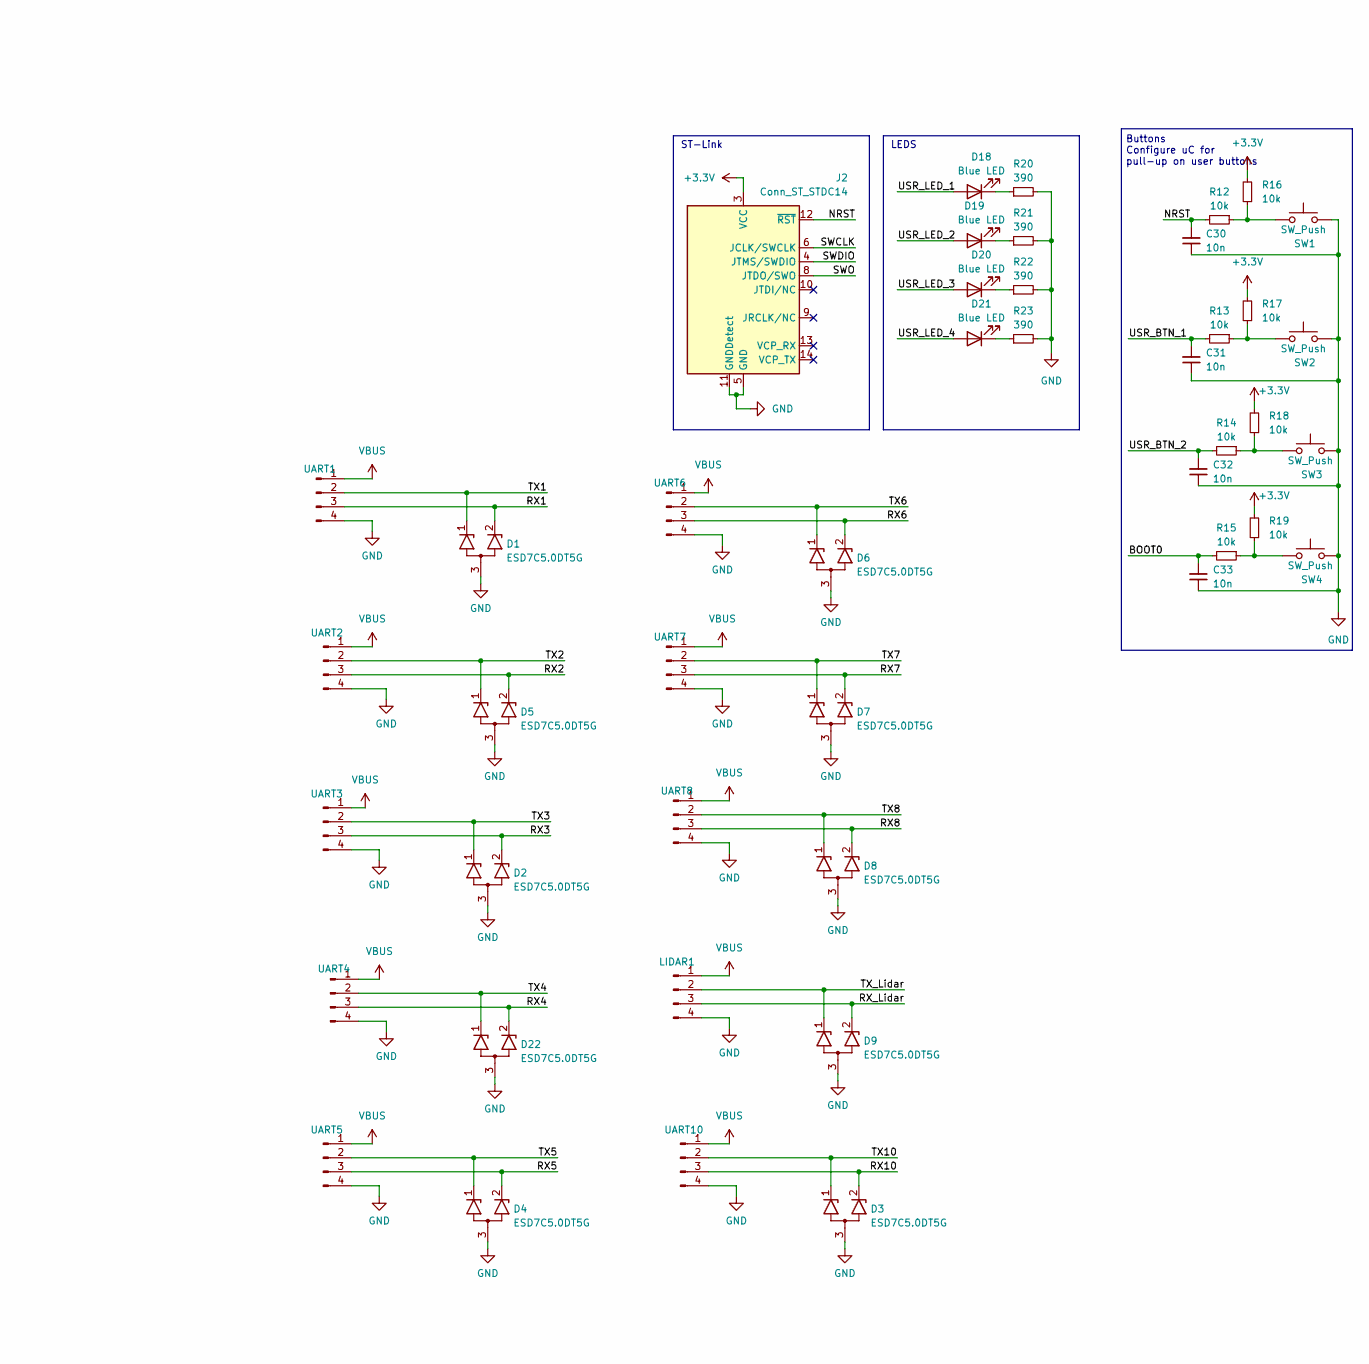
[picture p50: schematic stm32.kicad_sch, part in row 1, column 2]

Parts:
C12, C13, C14, C15, C16, C17, C18, C19, C20, C21, C22, C23, C24, C25, C26, C27, C28, C35, C36, C39, C40, C41: 100n; C_0402_1005Metric
C29, C37, C38, C45, C48: 10u; C_0603_1608Metric
C30, C31, C32, C33: 10n; C_0402_1005Metric
C34: 1u; C_0402_1005Metric
C42, C43, C44: 2.2u; C_0402_1005Metric
D1, D2, D3, D4, D5, D6, D7, D8, D9, D22: ESD7C5.0DT5G; SOT-416; Mouser Part Number 863-ESD7C5.0DT5G
D18, D19, D20, D21: Blue LED; LED_0603_1608Metric
J2: Conn_ST_STDC14; PinHeader_2x07_P1.27mm_Vertical_SMD
LIDAR1: Conn_01x04_Male; JST_EH_B4B-EH-A_1x04_P2.50mm_Vertical
R4, R12, R13, R14, R15, R16, R17, R18, R19: 10k; R_0402_1005Metric
R20, R21, R22, R23: 390; R_0402_1005Metric
SW1, SW2, SW3, SW4: SW_Push; 435451019820
U1: STM32H735IGTx; LQFP-176_24x24mm_P0.5mm
UART1, UART2, UART3, UART4, UART5, UART6, UART7, UART8, UART10: Conn_01x04_Male; JST_EH_B4B-EH-A_1x04_P2.50mm_Vertical

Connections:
+3.3V: C12.1, C13.1, C14.1, C15.1, C16.1, C17.1, C18.1, C19.1, C20.1, C21.1, C22.1, C23.1, C24.1, C25.1, C26.1, C27.1, C28.1, C29.1, C34.1, C35.1, C36.1, C37.1, C38.1, C40.1, C45.1, J2.3 (VCC), R16.2, R17.2, R18.2, R19.2, U1.7 (VDD), U1.8 (VBAT), U1.13 (VDD), U1.25 (VDD), U1.39 (VREF+), U1.40 (VDDA), U1.44 (VDD), U1.48 (VDD), U1.65 (VDD), U1.71 (VDD), U1.82 (VDDLDO), U1.84 (VDD), U1.92 (VDD), U1.99 (VDD), U1.105 (VDD), U1.113 (VDD), U1.121 (VDD33USB), U1.126 (VDD), U1.135 (VDDLDO), U1.136 (VDD), U1.152 (VDD), U1.160 (VDD), U1.175 (VDDLDO), U1.176 (VDD); also elsewhere on the board
+5V: C41.1, U1.120 (VDD50USB); also elsewhere on the board
/GPIO14_TXD: U1.128 (PA9); also elsewhere on the board
/GPIO15_RXD: U1.129 (PA10); also elsewhere on the board
/STM32H735/BOOT0: C33.2, R4.2, R15.2, U1.167 (BOOT0)
/STM32H735/NRST: C30.2, C39.2, J2.12 (~RST), R12.2, U1.33 (NRST)
/STM32H735/RX1: D1.2 (K2), U1.88 (PB15), UART1.3
/STM32H735/RX2: D5.2 (K2), U1.149 (PD6), UART2.3
/STM32H735/RX3: D2.2 (K2), U1.79 (PB11), UART3.3
/STM32H735/RX4: D22.2 (K2), U1.42 (PA1), UART4.3
/STM32H735/RX5: D4.2 (K2), U1.85 (PB12), UART5.3
/STM32H735/RX6: D6.2 (K2), U1.123 (PC7), UART6.3
/STM32H735/RX7: D7.2 (K2), U1.67 (PE7), UART7.3
/STM32H735/RX8: D8.2 (K2), U1.102 (PJ9), UART8.3
/STM32H735/RX10: D3.2 (K2), U1.1 (PE2), UART10.3
/STM32H735/RX_Lidar: D9.2 (K2), LIDAR1.3, U1.97 (PD14)
/STM32H735/SWCLK: J2.6 (JCLK/SWCLK), U1.138 (PA14(JTCK)
/STM32H735/SWDIO: J2.4 (JTMS/SWDIO), U1.132 (PA13(JTMS)
/STM32H735/SWO: J2.8 (JTDO/SWO), U1.162 (PB3(JTDO)
/STM32H735/TX1: D1.1 (K1), U1.87 (PB14), UART1.2
/STM32H735/TX2: D5.1 (K1), U1.148 (PD5), UART2.2
/STM32H735/TX3: D2.1 (K1), U1.78 (PB10), UART3.2
/STM32H735/TX4: D22.1 (K1), U1.41 (PA0), UART4.2
/STM32H735/TX5: D4.1 (K1), U1.86 (PB13), UART5.2
/STM32H735/TX6: D6.1 (K1), U1.122 (PC6), UART6.2
/STM32H735/TX7: D7.1 (K1), U1.68 (PE8), UART7.2
/STM32H735/TX8: D8.1 (K1), U1.101 (PJ8), UART8.2
/STM32H735/TX10: D3.1 (K1), U1.2 (PE3), UART10.2
/STM32H735/TX_Lidar: D9.1 (K1), LIDAR1.2, U1.98 (PD15)
/STM32H735/USR_BTN_1: C31.2, R13.2, U1.163 (PB4(NJTRST))
/STM32H735/USR_BTN_2: C32.2, R14.2, U1.164 (PB5)
/STM32H735/USR_LED_1: D18.2 (A), U1.18 (PF0)
/STM32H735/USR_LED_2: D19.2 (A), U1.19 (PF1)
/STM32H735/USR_LED_3: D20.2 (A), U1.20 (PF2)
/STM32H735/USR_LED_4: D21.2 (A), U1.21 (PF3)
GND: C12.2, C13.2, C14.2, C15.2, C16.2, C17.2, C18.2, C19.2, C20.2, C21.2, C22.2, C23.2, C24.2, C25.2, C26.2, C27.2, C28.2, C29.2, C30.1, C31.1, C32.1, C33.1, C34.2, C35.2, C36.2, C37.2, C38.2, C39.1, C40.2, C41.2, C42.2, C43.2, C44.2, C45.2, C48.2, D1.3 (A), D2.3 (A), D3.3 (A), D4.3 (A), D5.3 (A), D6.3 (A), D7.3 (A), D8.3 (A), D9.3 (A), D22.3 (A), J2.5 (GND), J2.7 (GND), J2.11 (GNDDetect), LIDAR1.4, R4.1, R20.2, R21.2, R22.2, R23.2, SW1.2, SW2.2, SW3.2, SW4.2, U1.6 (VSS), U1.12 (VSS), U1.14 (VSSSMPS), U1.15 (VLXSMPS), U1.16 (VDDSMPS), U1.17 (VFBSMPS), U1.24 (VSS), U1.38 (VSSA), U1.45 (VSS), U1.47 (VSS), U1.64 (VSS), U1.70 (VSS), U1.81 (VSS), U1.83 (VSS), U1.93 (VSS), U1.100 (VSS), U1.106 (VSS), U1.112 (VSS), U1.119 (VSS), U1.134 (VSS), U1.137 (VSS), U1.151 (VSS), U1.159 (VSS), U1.173 (VSS), U1.174 (PDR_ON), UART1.4, UART2.4, UART3.4, UART4.4, UART5.4, UART6.4, UART7.4, UART8.4, UART10.4; also elsewhere on the board
unnamed: C42.1, C48.1, U1.80 (VCAP)
unnamed: C43.1, U1.133 (VCAP)
unnamed: C44.1, U1.172 (VCAP)
unnamed: D18.1 (K), R20.1
unnamed: D19.1 (K), R21.1
unnamed: D20.1 (K), R22.1
unnamed: D21.1 (K), R23.1
unnamed: R12.1, R16.1, SW1.1
unnamed: R13.1, R17.1, SW2.1
unnamed: R14.1, R18.1, SW3.1
unnamed: R15.1, R19.1, SW4.1
VBUS: LIDAR1.1, UART1.1, UART2.1, UART3.1, UART4.1, UART5.1, UART6.1, UART7.1, UART8.1, UART10.1; also elsewhere on the board

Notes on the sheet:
LEDS
17 VDD
Buttons Configure uC for pull-up on user buttons
ST-Link

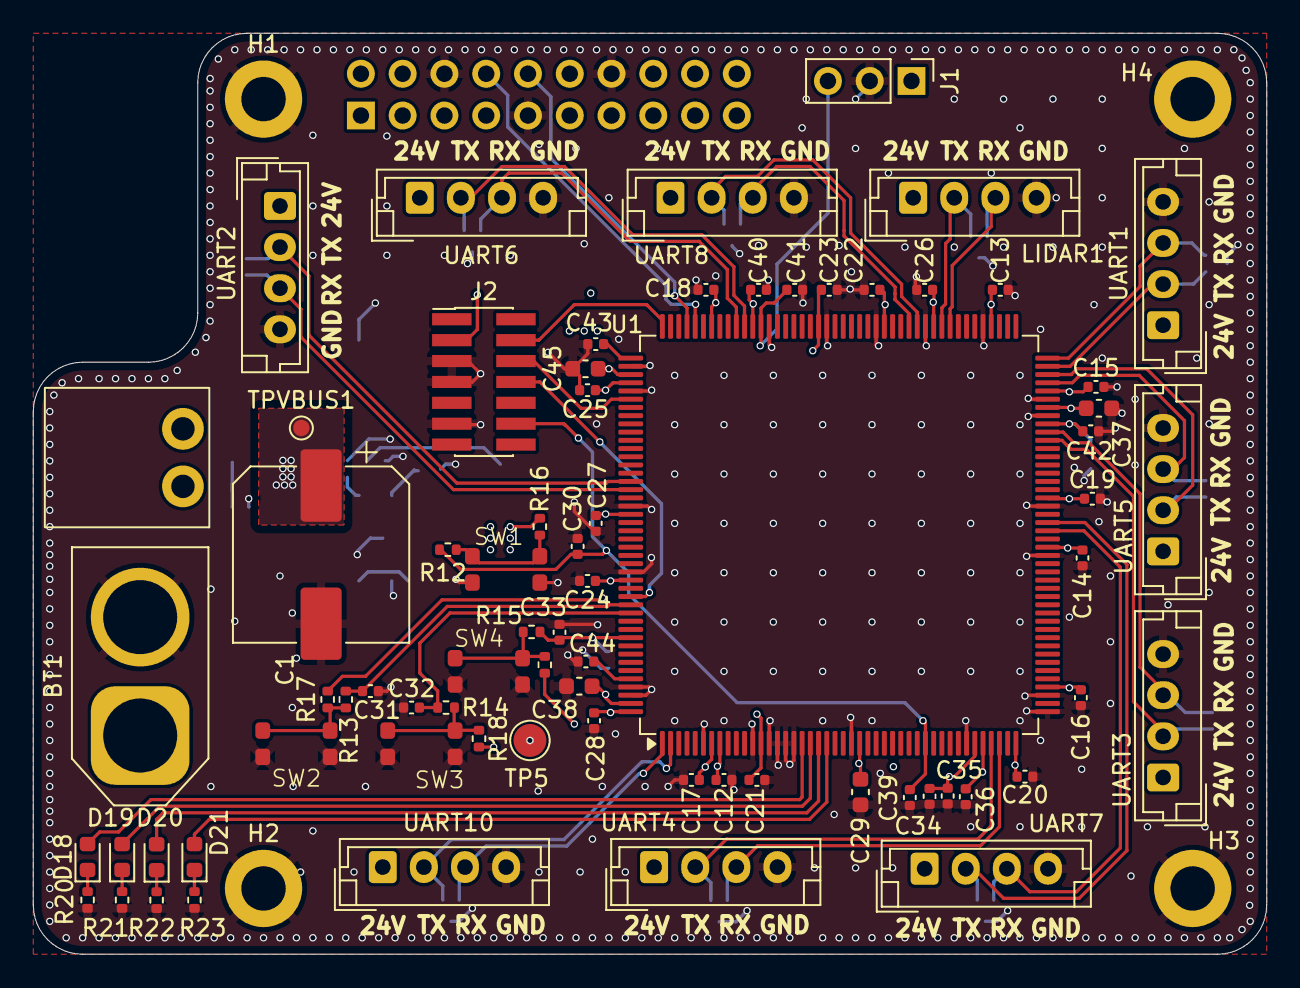
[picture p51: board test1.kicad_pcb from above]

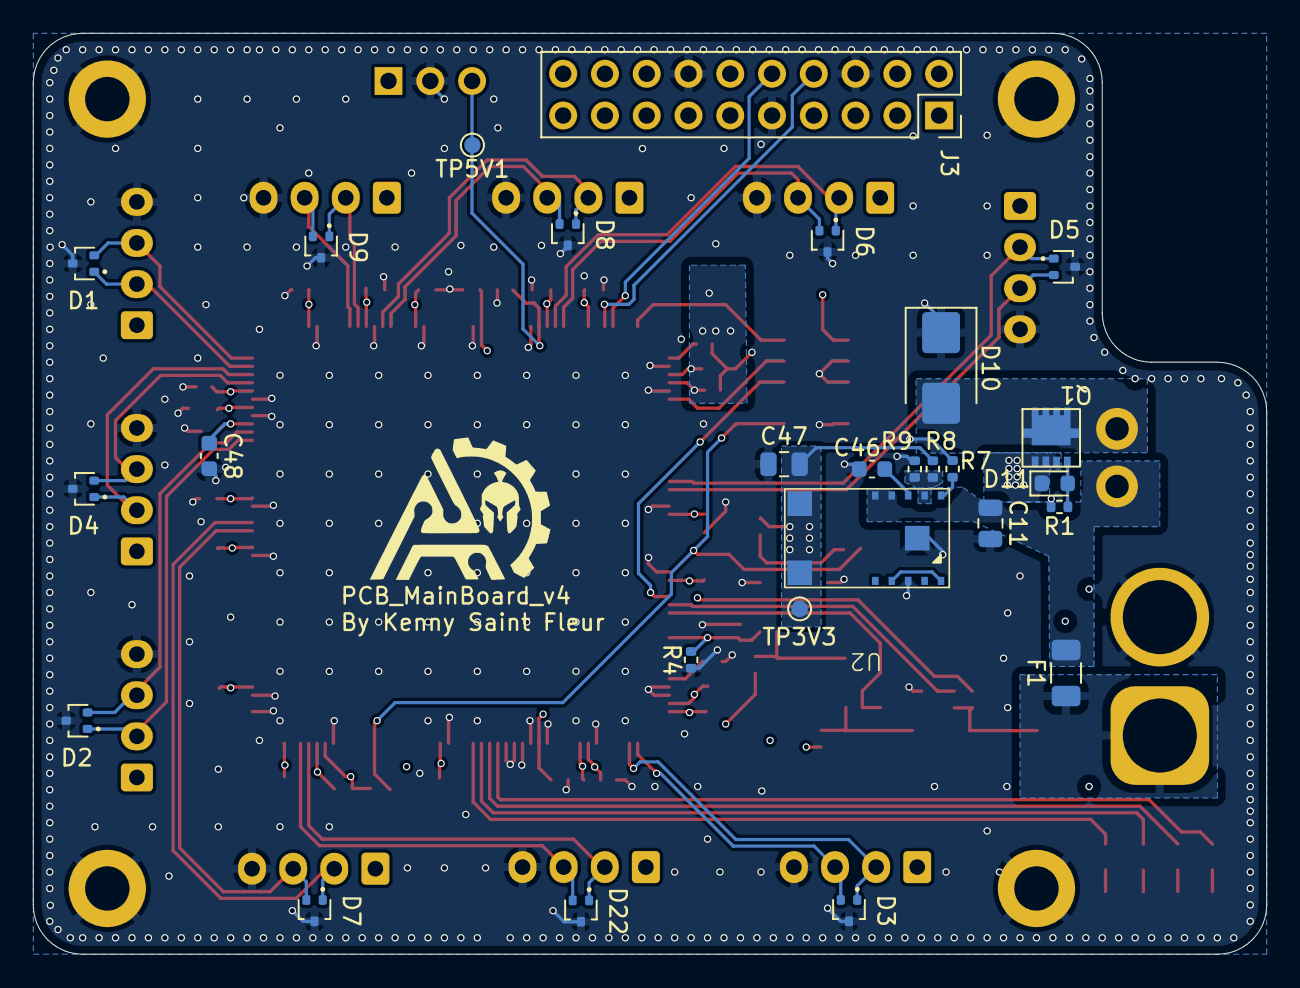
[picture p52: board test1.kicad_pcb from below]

Board: 4 copper layers, 75.0 x 56.0 mm, 103 parts (27 on the bottom side), 56 nets.

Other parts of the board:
TP3V3: 3.3V; TestPoint_Pad_D1.0mm
TP5: TestPoint; TestPoint_Pad_D2.0mm

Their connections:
+3.3V: TP3V3.1, TP5.1; also elsewhere on the board

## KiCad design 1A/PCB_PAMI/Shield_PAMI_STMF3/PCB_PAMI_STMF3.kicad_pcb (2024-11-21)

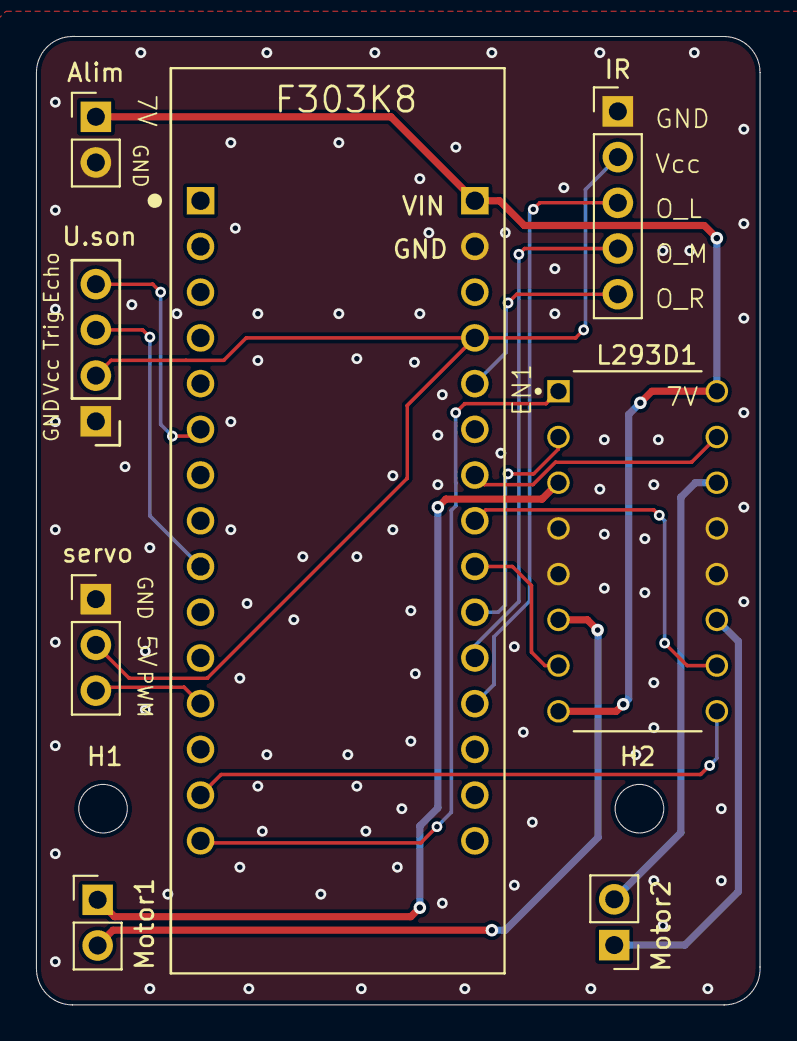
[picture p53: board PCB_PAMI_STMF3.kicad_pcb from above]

Board: 2 copper layers, 40.2 x 53.8 mm, 10 parts (0 on the bottom side), 19 nets.

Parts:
Alim: PinHeader_1x02_P2.54mm_Vertical
F303K8: MODULE_NUCLEO-F303K8
H1, H2: MountingHole_Pad; MountingHole_2.7mm_M2.5
IR: PinHeader_1x05_P2.54mm_Vertical
L293D1: L293D; L293D_Motor_Driver
Motor1, Motor2: PinHeader_1x02_P2.54mm_Vertical
U.son: PinHeader_1x04_P2.54mm_Vertical
servo: PinHeader_1x03_P2.54mm_Vertical

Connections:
/5V: F303K8.4_4 (5V), IR.2 (VCC), U.son.2 (Vcc), servo.1 (GND)
/7V: Alim.1 (7V), F303K8.4_1 (VIN), L293D1.8 (VS), L293D1.16 (VSS)
/EN1: F303K8.3_15 (PB_4), L293D1.1 (ENABLE1)
/EN2: F303K8.3_14 (PB_5), L293D1.9 (ENABLE2)
/Echo: F303K8.3_6 (PB_0), U.son.4 (Echo)
/GND: Alim.2 (GND), F303K8.4_2 (GND), IR.1 (GND), L293D1.4 (GND), L293D1.5 (GND), L293D1.12 (GND), L293D1.13 (GND), U.son.1 (GND), servo.2 (5V)
/IN1: F303K8.4_10 (PA_3), L293D1.2 (INPUT1)
/IN2: F303K8.4_9 (PA_4), L293D1.7 (INPUT2)
/IN3: F303K8.4_8 (PA_5), L293D1.10 (INPUT3)
/IN4: F303K8.4_7 (PA_6), L293D1.15 (INPUT4)
/O_L: F303K8.4_12 (PA_0), IR.3 (O_L)
/O_M: F303K8.4_11 (PA_1), IR.4 (O_M)
/O_R: F303K8.4_5 (PA_2), IR.5 (O_R)
/Trig: F303K8.3_9 (PB_1), U.son.3 (Trig)
/out1: L293D1.3 (OUTPUT1), Motor1.1 (input1)
/out2: L293D1.6 (OUTPUT2), Motor1.2 (input2)
/out3: L293D1.11 (OUTPUT3), Motor2.1 (input1)
/out4: L293D1.14 (OUTPUT4), Motor2.2 (input2)
/pwm_servo: F303K8.3_12 (PA_8), servo.3 (PWM)

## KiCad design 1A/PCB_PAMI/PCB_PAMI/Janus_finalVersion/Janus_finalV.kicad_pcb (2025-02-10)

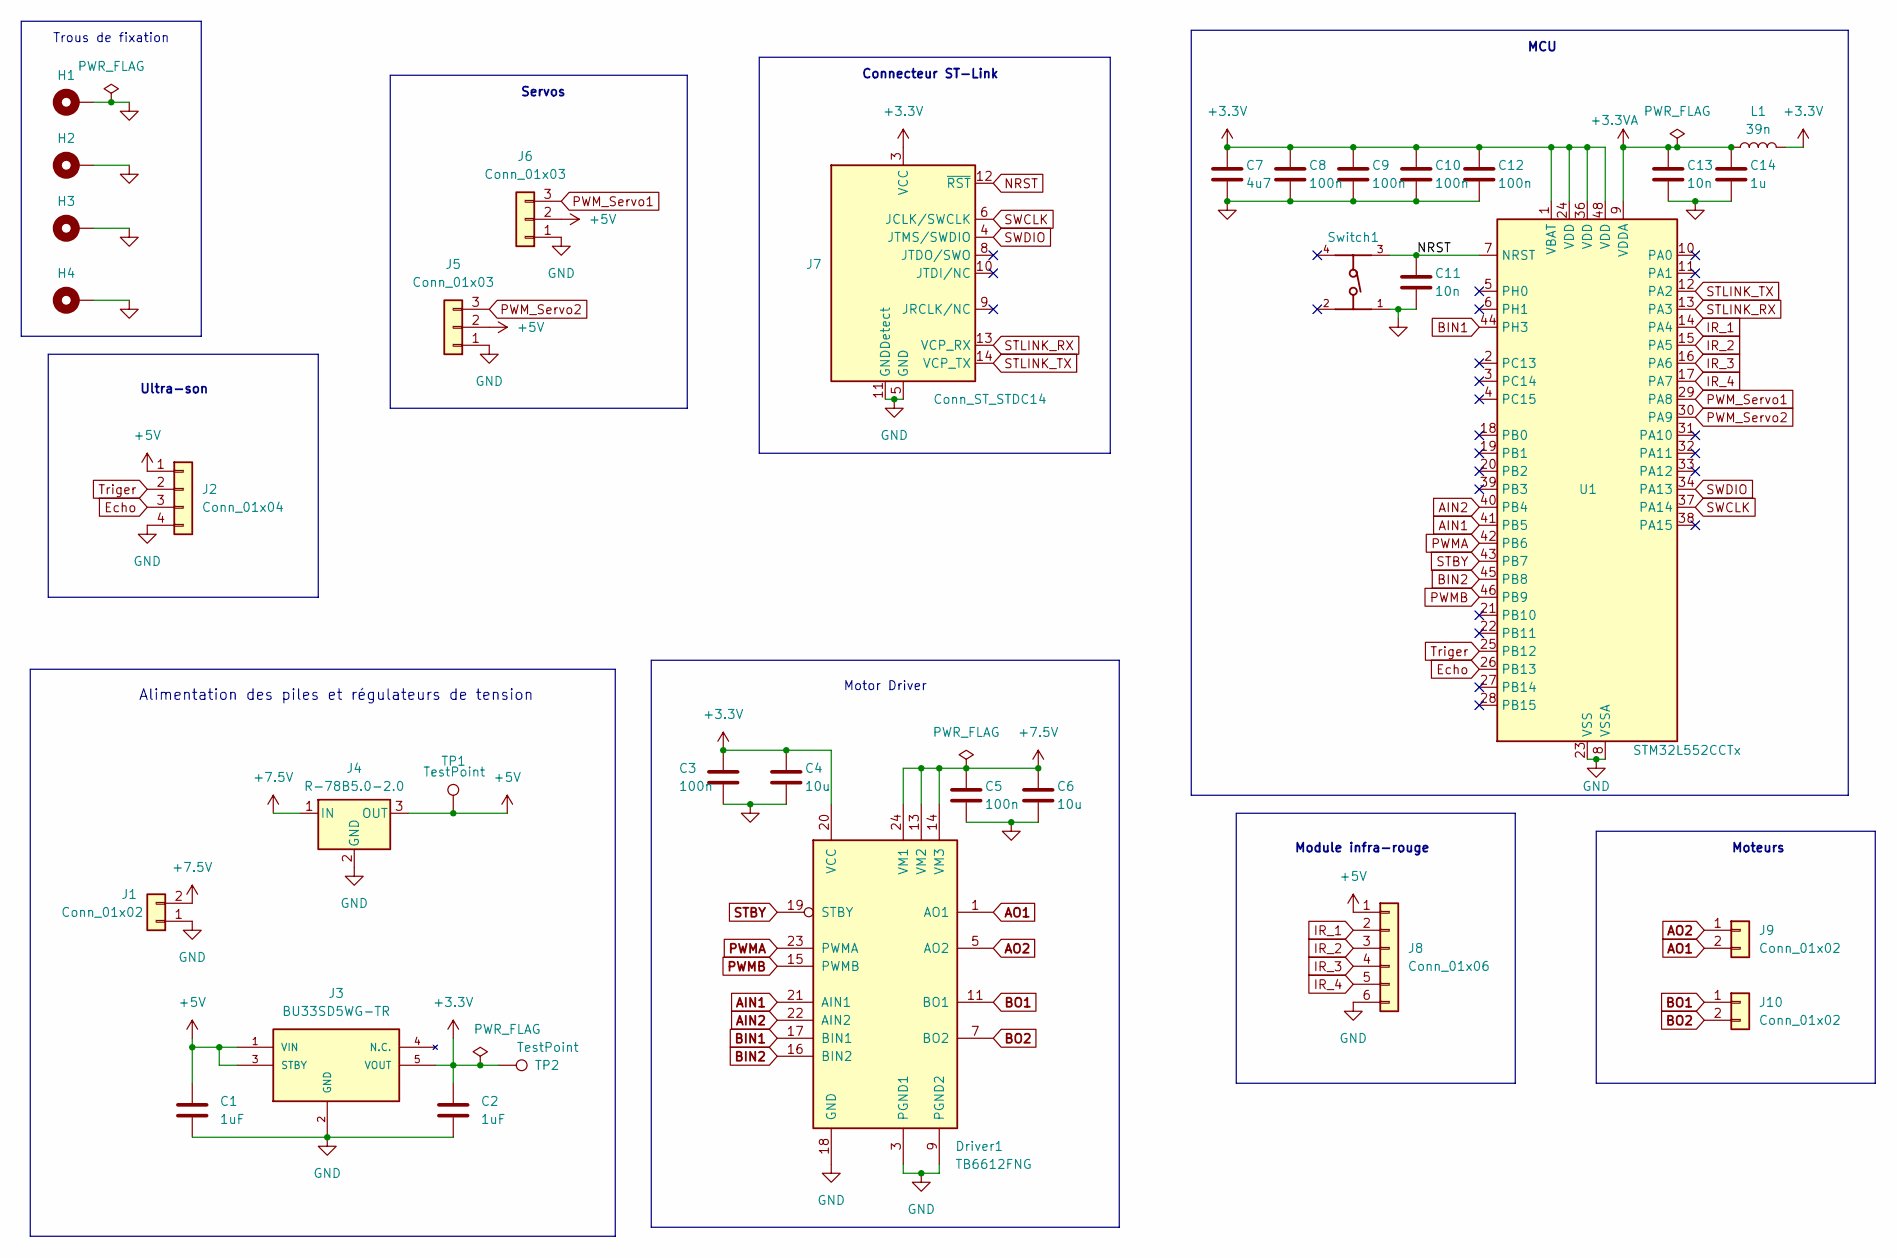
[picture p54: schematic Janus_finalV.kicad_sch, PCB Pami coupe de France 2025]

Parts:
C1, C2: 1uF; C_0603_1608Metric_Pad1.08x0.95mm_HandSolder
C3, C5, C8, C9, C10, C12: 100n; C_0402_1005Metric
C4, C6: 10u; C_0805_2012Metric
C7: 4u7; C_0805_2012Metric
C11, C13: 10n; C_0402_1005Metric
C14: 1u; C_0402_1005Metric
Driver1: TB6612FNG; SSOP-24_5.3x8.2mm_P0.65mm
H1, H2, H3, H4: MountingHole_Pad; MountingHole_2.7mm_M2.5_Pad
J1: Conn_01x02; JST_XH_S2B-XH-A-1_1x02_P2.50mm_Horizontal
J2: Conn_01x04; JST_PH_B4B-PH-K_1x04_P2.00mm_Vertical
J3: BU33SD5WG-TR; SOT95P280X125-5N; Mouser_Part_Number 755-BU33SD5WG-TR
J4: R-78B5.0-2.0; Converter_DCDC_RECOM_R-78B-2.0_THT
J5, J6: Conn_01x03; JST_XH_B3B-XH-A_1x03_P2.50mm_Vertical
J7: Conn_ST_STDC14; PinHeader_2x07_P1.27mm_Vertical_SMD
J8: Conn_01x06; JST_XH_S6B-XH-A-1_1x06_P2.50mm_Horizontal
J9, J10: Conn_01x02; JST_XH_B2B-XH-A_1x02_P2.50mm_Vertical
L1: 39n; L_0603_1608Metric
Switch1: 430471025826; PART-NUMBER 430471025826
TP1, TP2: TestPoint; TestPoint_Pad_D2.0mm
U1: STM32L552CCTx; LQFP-48_7x7mm_P0.5mm

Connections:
+3.3V: C2.1, C3.1, C4.1, C7.1, C8.1, C9.1, C10.1, C12.1, Driver1.20 (VCC), J3.5 (VOUT), J7.3 (VCC), L1.2, TP2.1, U1.1 (VBAT), U1.24 (VDD), U1.36 (VDD), U1.48 (VDD)
+3.3VA: C13.1, C14.1, L1.1, U1.9 (VDDA)
+5V: C1.1, J2.1, J3.1 (VIN), J3.3 (STBY), J4.3 (OUT), J5.2, J6.2, J8.1, TP1.1
+7.5V: C5.1, C6.1, Driver1.13 (VM2), Driver1.14 (VM3), Driver1.24 (VM1), J1.2, J4.1 (IN)
AIN1: Driver1.21 (AIN1), U1.41 (PB5)
AIN2: Driver1.22 (AIN2), U1.40 (PB4)
AO1: Driver1.1 (AO1), Driver1.2 (AO1), J9.2
AO2: Driver1.5 (AO2), Driver1.6 (AO2), J9.1
BIN1: Driver1.17 (BIN1), U1.44 (PH3)
BIN2: Driver1.16 (BIN2), U1.45 (PB8)
BO1: Driver1.11 (BO1), Driver1.12 (BO1), J10.1
BO2: Driver1.7 (BO2), Driver1.8 (BO2), J10.2
Echo: J2.3, U1.26 (PB13)
GND: C1.2, C2.2, C3.2, C4.2, C5.2, C6.2, C7.2, C8.2, C9.2, C10.2, C11.2, C12.2, C13.2, C14.2, Driver1.3 (PGND1), Driver1.4 (PGND1), Driver1.9 (PGND2), Driver1.10 (PGND2), Driver1.18 (GND), H1.1, H2.1, H3.1, H4.1, J1.1, J2.4, J3.2 (GND), J4.2 (GND), J5.1, J6.1, J7.5 (GND), J7.7 (GND), J7.11 (GNDDetect), J8.6, Switch1.1, U1.8 (VSSA), U1.23 (VSS), U1.35 (VSS), U1.47 (VSS)
IR_1: J8.2, U1.14 (PA4)
IR_2: J8.3, U1.15 (PA5)
IR_3: J8.4, U1.16 (PA6)
IR_4: J8.5, U1.17 (PA7)
NRST: C11.1, J7.12 (~RST), Switch1.3, U1.7 (NRST)
PWMA: Driver1.23 (PWMA), U1.42 (PB6)
PWMB: Driver1.15 (PWMB), U1.46 (PB9)
PWM_Servo1: J6.3, U1.29 (PA8)
PWM_Servo2: J5.3, U1.30 (PA9)
STBY: Driver1.19 (STBY), U1.43 (PB7)
STLINK_RX: J7.13 (VCP_RX), U1.13 (PA3)
STLINK_TX: J7.14 (VCP_TX), U1.12 (PA2)
SWCLK: J7.6 (JCLK/SWCLK), U1.37 (PA14)
SWDIO: J7.4 (JTMS/SWDIO), U1.34 (PA13)
Triger: J2.2, U1.25 (PB12)

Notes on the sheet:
Trous de fixation
Servos
Moteurs
Module infra-rouge
Connecteur ST-Link
Ultra-son
Alimentation des piles et régulateurs de tension
Motor Driver
MCU



Board: 4 copper layers, 41.0 x 52.4 mm, 34 parts (8 on the bottom side), 29 nets.

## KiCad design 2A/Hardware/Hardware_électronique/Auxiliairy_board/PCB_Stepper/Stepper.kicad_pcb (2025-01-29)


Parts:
C1: 2u2; C_0402_1005Metric
C2, C3, C13, C14, C15: 100n; C_0603_1608Metric
C4, C16: 100u; CP_Elec_10x10.5
C8: 10u; C_0805_2012Metric_Pad1.18x1.45mm_HandSolder
C9: 22u; C_0805_2012Metric
C10: 100n; C_0402_1005Metric
C11: 4.7u; C_0402_1005Metric
C12: 22n; C_0603_1608Metric
C17: 22n; C_0603_1608Metric_Pad1.08x0.95mm_HandSolder
C18: 100n; C_0603_1608Metric_Pad1.08x0.95mm_HandSolder
D1: ESD7C5.0DT5G; SOT-416; Mouser Part Number 863-ESD7C5.0DT5G
H1, H2, H3, H4: MountingHole_Pad; MountingHole_2.7mm_M2.5_ISO7380_Pad
J1: UART_IN; JST_EH_B4B-EH-A_1x04_P2.50mm_Vertical
J2: Conn_ST_STDC14; PinHeader_2x07_P1.27mm_Vertical_SMD
J3, J4: Conn_01x04; JST_EH_B4B-EH-A_1x04_P2.50mm_Vertical
J5: FinCourse1; JST_EH_B2B-EH-A_1x02_P2.50mm_Vertical
J6: FinCourse2; JST_EH_B2B-EH-A_1x02_P2.50mm_Vertical
TP1: 5V; TestPoint_Pad_D2.0mm
TP2: 3.3V; TestPoint_Pad_D2.0mm
U1, U2: TMC2225; HTSSOP-28-1EP_4.4x9.7mm_P0.65mm_EP2.75x6.2mm_ThermalVias
U4: AZ1117-3.3; SOT-223-3_TabPin2
U5: STM32G071KBUx; QFN-32-1EP_5x5mm_P0.5mm_EP3.45x3.45mm

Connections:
+3.3V: C9.1, C10.1, C11.1, J2.3 (VCC), TP2.1, U1.16 (VCC_IO), U1.19 (SPREAD), U1.25 (MS1_AD0), U2.16 (VCC_IO), U2.19 (SPREAD), U2.25 (MS1_AD0), U4.2 (VO), U5.4 (VDD)
+5V: C1.2, C8.1, TP1.1, U2.15 (5VOUT), U4.3 (VI)
/Course1: J5.1, U5.23 (PA12/PA10)
/Course2: J6.1, U5.9 (PA2)
/DIAG1: U1.18 (DIAG), U5.18 (PA8)
/DIAG2: U2.18 (DIAG), U5.10 (PA3)
/NRST: J2.12 (~RST), U5.6 (PF2)
/RX: D1.1 (K1), J1.2, U5.31 (PB7)
/SWCLK: J2.6 (JCLK/SWCLK), U5.25 (PA14)
/SWDIO: J2.4 (JTMS/SWDIO), U5.24 (PA13)
/TX: D1.2 (K2), J1.3, U5.30 (PB6)
/U1_OA1: J4.2, U1.7 (OA1)
/U1_OA2: J4.1, U1.5 (OA2)
/U1_OB1: J4.3, U1.8 (OB1)
/U1_OB2: J4.4, U1.10 (OB2)
/U2_OA1: J3.2, U2.7 (OA1)
/U2_OA2: J3.1, U2.5 (OA2)
/U2_OB1: J3.3, U2.8 (OB1)
/U2_OB2: J3.4, U2.10 (OB2)
/dir1: U1.20 (DIR), U5.19 (PA9/UCPD1_DBCC1)
/dir2: U2.20 (DIR), U5.11 (PA4)
/index1: U1.27 (INDEX), U5.22 (PA11/PA9)
/index2: U2.27 (INDEX), U5.14 (PA7)
/step1: U1.22 (STEP), U5.21 (PA10/UCPD1_DBCC2)
/step2: U2.22 (STEP), U5.13 (PA6)
/~EN1: U1.21 (~EN), U5.20 (PC6)
/~EN2: U2.21 (~EN), U5.12 (PA5)
GND: C1.1, C2.2, C3.2, C4.2, C8.2, C9.2, C10.2, C11.2, C14.2, C15.2, C16.2, D1.3 (A), H1.1, H2.1, H3.1, H4.1, J1.4, J2.5 (GND), J2.7 (GND), J2.11 (GNDDetect), J5.2, J6.2, U1.6 (BRA), U1.9 (BRB), U1.14 (GND), U1.26 (MS2_AD1), U1.28 (GND), U1.29 (GND), U2.6 (BRA), U2.9 (BRB), U2.14 (GND), U2.26 (MS2_AD1), U2.28 (GND), U2.29 (GND), U4.1 (GND), U5.5 (VSS), U5.33 (VSS)
unnamed: C17.2, U1.2 (CPI)
unnamed: C17.1, U1.1 (CPO)
unnamed: C18.2, U1.3 (VCP)
unnamed: C12.2, U2.2 (CPI)
unnamed: C12.1, U2.1 (CPO)
unnamed: C13.2, U2.3 (VCP)
VBUS: C2.1, C3.1, C4.1, C13.1, C14.1, C15.1, C16.1, C18.1, J1.1, U1.4 (VS), U1.11 (VS), U2.4 (VS), U2.11 (VS)

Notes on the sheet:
Motor drivers
Conn_Uart
Connecteurs fin de course
Mounting Holes
Connectuers moteurs NEMA 11
LDO +5V-> +3.3V
ST-Link
MCU STM32G071KBU6TR



Board: 4 copper layers, 50.0 x 43.0 mm, 32 parts (12 on the bottom side), 35 nets.

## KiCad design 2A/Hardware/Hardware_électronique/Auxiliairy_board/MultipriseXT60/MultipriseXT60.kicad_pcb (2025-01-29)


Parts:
ARU2: 180G-2; AMASS_XT60-F_1x02_P7.20mm_Vertical
H5, H6, H7, H8: MountingHole_Pad; MountingHole_3.2mm_M3_Pad_Via
J1, J2, J3, J4, J5, J6, J7, J8: Conn_01x02_Pin; AMASS_XT60-F_1x02_P7.20mm_Vertical

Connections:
BAT+: ARU2.1, J3.2, J4.2, J5.2, J6.2, J7.2, J8.2
GND: H5.1, H6.1, H7.1, H8.1, J1.1, J2.1, J3.1, J4.1, J5.1, J6.1, J7.1, J8.1
SEC: ARU2.2, J1.2, J2.2

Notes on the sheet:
Mounting holes

Board: 2 copper layers, 13 parts (0 on the bottom side), 3 nets, no tracks yet.

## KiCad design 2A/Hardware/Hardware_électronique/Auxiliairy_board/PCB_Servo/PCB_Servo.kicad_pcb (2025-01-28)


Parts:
C1: 4.7u; C_0402_1005Metric
C2, C3, C7: 100n; C_0402_1005Metric
C4, C5: 10u; C_0805_2012Metric
C6: 2.2n; C_0402_1005Metric
C8, C9, C10: 22u; C_0805_2012Metric
C17: 10u; C_0805_2012Metric_Pad1.18x1.45mm_HandSolder
C18: 22u; C_0805_2012Metric_Pad1.18x1.45mm_HandSolder
D1: ESD7C5.0DT5G; SOT-416; Mouser Part Number 863-ESD7C5.0DT5G
H1, H2, H3: MountingHole_Pad; MountingHole_2.7mm_M2.5_Pad
J9: UART_IN; JST_EH_B4B-EH-A_1x04_P2.50mm_Vertical
J10: Conn_ST_STDC14; PinHeader_2x07_P1.27mm_Vertical_SMD
L1: 4.7u; PA5432.472NLT; MPN 74404084220
PA7, PA8, PA10, PA11: Conn_01x03_Pin; JST_EH_B3B-EH-A_1x03_P2.50mm_Vertical
PB0, PB10, PB14, PB15: Conn_01x03_Pin; JST_EH_B3B-EH-A_1x03_P2.50mm_Vertical
R1: 200k; R_0402_1005Metric
R2: 19.6k; R_0402_1005Metric
R3: 82k; R_0402_1005Metric
R4: 10k; R_0402_1005Metric
TP1: TestPoint; TestPoint_Pad_D2.0mm
U1: STM32G071CBUx; QFN-48-1EP_7x7mm_P0.5mm_EP5.6x5.6mm
U2: AZ1117-3.3; SOT-223
U3: AP64500Q; SOIC-8-1EP_3.9x4.9mm_P1.27mm_EP2.95x4.9mm_Mask2.71x3.4mm

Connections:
+3.3V: C1.1, C2.1, C3.1, C18.1, J10.3 (VCC), U1.4 (VBAT), U1.5 (VREF+), U1.6 (VDD), U2.2 (VO), U2.4 (VOUT)
+7.5V: C8.1, C9.1, C10.1, C17.1, L1.2, PA7.1, PA8.1, PA10.1, PA11.1, PB0.1, PB10.1, PB14.1, PB15.1, TP1.1, U2.3 (VI)
/NRST: J10.12 (~RST), U1.10 (PF2)
/PWM1: PA8.2, U1.28 (PA8)
/PWM2: PA11.2, U1.33 (PA11/PA9)
/PWM3: PA10.2, U1.32 (PA10/UCPD1_DBCC2)
/PWM4: PB14.2, U1.26 (PB14)
/PWM5: PA7.2, U1.18 (PA7)
/PWM6: PB0.2, U1.19 (PB0)
/PWM7: PB15.2, U1.27 (PB15)
/PWM8: PB10.2, U1.22 (PB10)
/RX: D1.1 (K1), J9.2, U1.46 (PB7)
/SW: C7.2, L1.1, R3.1, U3.8 (SW)
/SWCLK: J10.6 (JCLK/SWCLK), U1.36 (PA14)
/SWDIO: J10.4 (JTMS/SWDIO), U1.35 (PA13)
/TX: D1.2 (K2), J9.3, U1.45 (PB6)
/USART2_RX: J10.13 (VCP_RX), U1.13 (PA2)
/USART2_TX: J10.14 (VCP_TX), U1.14 (PA3)
GND: C1.2, C2.2, C3.2, C4.2, C5.2, C6.2, C8.2, C9.2, C10.2, C17.2, C18.2, D1.3 (A), H1.1, H2.1, H3.1, J9.4, J10.5 (GND), J10.7 (GND), J10.11 (GNDDetect), PA7.3, PA8.3, PA10.3, PA11.3, PB0.3, PB10.3, PB14.3, PB15.3, R1.2, R4.2, U1.7 (VSS), U1.49 (VSS), U2.1 (GND), U3.7 (GND), U3.9 (EPad)
unnamed: C6.1, R2.2
unnamed: C7.1, U3.1 (BST)
unnamed: R2.1, U3.6 (COMP)
unnamed: R3.2, R4.1, U3.5 (FB)
unnamed: R1.1, U3.4 (RT/CLK)
VBUS: C4.1, C5.1, J9.1, U3.2 (VIN), U3.3 (EN)

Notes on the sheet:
Converter +7.5V -> +3.3V
Mounting Hole
Buck 25.2V -> 7.5V
7.35V
Courant?
Conn_Uart
STM32G071
ST-Link
Conn PWM


Board: 2 copper layers, 38.8 x 40.2 mm, 35 parts (0 on the bottom side), 25 nets.

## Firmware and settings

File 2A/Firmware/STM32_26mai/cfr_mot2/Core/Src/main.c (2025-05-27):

/**
  ******************************************************************************
  * @file           : main.c
  * @brief          : Main program for odometry and motor control of a robot
  *                  using an STM32L476 microcontroller with AMT102-V encoders.
  *                  Combines precise odometry with independent wheel control.
  *                  Modified to address 0.06 m offset in movement.
  ******************************************************************************
  * @attention
  *
  * Copyright (c) 2025 STMicroelectronics.
  * All rights reserved.
  *
  * This software is licensed under terms that can be found in the LICENSE file
  * in the root directory of this software component.
  * If no LICENSE file comes with this software, it is provided AS-IS.
  *
  ******************************************************************************
  */

/* Includes ------------------------------------------------------------------*/
#include "main.h"

/* Private includes ----------------------------------------------------------*/
#include <string.h>
#include <stdio.h>
#include <math.h>
#include <stdbool.h>
#include "servo.h"
#include "maxon.h"

/* Private defines -----------------------------------------------------------*/
#define ENCODER_COUNTS_PER_REV 4096      // Encoder resolution (PPR * 4, PPR = 1024)
#define WHEEL_DIAMETER 0.076f            // Adjusted wheel diameter in meters (80 mm, calibrated)
#define WHEEL_BASE 0.240f                // Distance between wheels in meters
#define WHEEL_CIRCUMFERENCE (3.1416f * WHEEL_DIAMETER) // Wheel circumference (pi * diameter) in meters
#define ENCODER_TOLERANCE 5              // Encoder tolerance for target position
#define OFFSET_CORRECTION 1027           // Encoder count offset correction (~0.06 m)

/* Private variables ---------------------------------------------------------*/
UART_HandleTypeDef hlpuart1;             // UART for receiving commands
UART_HandleTypeDef huart4;               // UART for servo communication
UART_HandleTypeDef huart5;               // UART for odometry output
UART_HandleTypeDef huart1;               // UART for stepper motor 1
UART_HandleTypeDef huart2;               // UART for debug console
UART_HandleTypeDef huart3;               // UART for stepper motor 2

TIM_HandleTypeDef htim1;                 // Timer for right wheel encoder
TIM_HandleTypeDef htim2;                 // Timer for PWM motor control
TIM_HandleTypeDef htim3;                 // Timer for left wheel encoder

/* Private variables for odometry and control */
char rx_data[27];                        // Buffer for received UART data
float x = 0.0f;                          // Robot X position (meters)
float y = 0.0f;                          // Robot Y position (meters)
float theta = 0.0f;                      // Robot orientation (radians)
int16_t prev_left = 0;                   // Previous left encoder value
int16_t prev_right = 0;                  // Previous right encoder value
uint32_t last_update_time = 0;           // Last control loop update time (ms)

float K_p = 300.0f;                      // Proportional gain for PI controller
float K_i = 200.0f;                      // Integral gain for PI controller
float e_sum = 0.0f;                      // Cumulative error for PI integral term
int v_L_base = 0;                        // Base speed for left motor
int v_R_base = 0;                        // Base speed for right motor
uint8_t inv_L = 0;                       // Left motor direction (0 = forward, 1 = reverse)
uint8_t inv_R = 0;                       // Right motor direction (0 = forward, 1 = reverse)
bool is_straight = false;                // Flag for straight-line motion
int s = 1;                               // Direction multiplier for straight motion (1 or -1)
const float right_motor_compensation = 0.81f; // Right motor speed compensation factor

bool position_control_active = false;     // Flag for active position control
bool control_locked = false;              // Lock control after reaching targets
int32_t target_left = 0;                 // Target position for left encoder (counts)
int32_t target_right = 0;                // Target position for right encoder (counts)
int32_t origin_left = 0;                 // Initial left encoder position
int32_t origin_right = 0;                // Initial right encoder position
const int low_speed = 200;               // Base speed for motors

float total_dist_left = 0.0f;            // Total distance traveled by left wheel (meters)
float total_dist_right = 0.0f;           // Total distance traveled by right wheel (meters)

uint8_t left_reached_count = 0;          // Counter for left wheel target reached
uint8_t right_reached_count = 0;         // Counter for right wheel target reached

/* Private function prototypes -----------------------------------------------*/
void SystemClock_Config(void);
static void MX_GPIO_Init(void);
static void MX_TIM2_Init(void);
static void MX_LPUART1_UART_Init(void);
static void MX_TIM1_Init(void);
static void MX_USART2_UART_Init(void);
static void MX_USART3_UART_Init(void);
static void MX_UART4_Init(void);
static void MX_USART1_UART_Init(void);
static void MX_TIM3_Init(void);
static void MX_UART5_Init(void);

/* Redirect printf to UART2 for debug output */
int __io_putchar(int ch) {
    HAL_UART_Transmit(&huart2, (uint8_t *)&ch, 1, HAL_MAX_DELAY);
    return ch;
}

/**
  * @brief  The application entry point.
  * @retval int
  */
int main(void)
{
    /* Initialize HAL */
    HAL_Init();

    /* Configure system clock */
    SystemClock_Config();

    /* Initialize peripherals */
    MX_GPIO_Init();
    MX_TIM2_Init();
    MX_LPUART1_UART_Init();
    MX_TIM1_Init();
    MX_USART2_UART_Init();
    MX_USART3_UART_Init();
    MX_UART4_Init();
    MX_USART1_UART_Init();
    MX_TIM3_Init();
    MX_UART5_Init();

    /* Start PWM for motor control */
    HAL_TIM_PWM_Start(&htim2, TIM_CHANNEL_3);
    HAL_TIM_PWM_Start(&htim2, TIM_CHANNEL_4);

    /* Start UART reception in interrupt mode */
    HAL_UART_Receive_IT(&hlpuart1, (uint8_t *)rx_data, sizeof(rx_data));

    /* Start encoders for both wheels */
    HAL_TIM_Encoder_Start(&htim3, TIM_CHANNEL_ALL);
    HAL_TIM_Encoder_Start(&htim1, TIM_CHANNEL_ALL);

    /* Initialize encoder values */
    prev_left = (int16_t)__HAL_TIM_GET_COUNTER(&htim3);
    prev_right = (int16_t)__HAL_TIM_GET_COUNTER(&htim1);
    origin_left = prev_left;
    origin_right = prev_right;

    while (1)
    {
        /* Find start of UART frame (marked by '>') */
        int offset = -1;
        for (int j = 0; j < sizeof(rx_data); j++) {
            if (rx_data[j] == '>') {
                offset = j;
                break;
            }
        }

        /* Process UART frame if valid */
        if (offset >= 0) {
            /* Copy data for console output */
            char console_data[29];
            for (int i = 0; i < 27; i++) {
                console_data[i] = rx_data[(offset + i) % 27];
            }
            console_data[27] = '\r';
            console_data[28] = '\n';
            HAL_UART_Transmit(&huart2, (uint8_t *)console_data, 29, HAL_MAX_DELAY);

            /* Extract right motor distance (mot_maxon_dataD) */
            char mot_maxon_dataD[5];
            for (int i = 0; i < 4; i++) {
                mot_maxon_dataD[i] = rx_data[(offset + 2 + i) % 27];
            }
            mot_maxon_dataD[4] = '\0';
            int target_mm_D = atoi(mot_maxon_dataD);
            if (target_mm_D < 0) target_mm_D = 0;

            /* Extract right motor direction (inv_d) */
            int inv_d = rx_data[(offset + 1) % 27] - '0';
            if (inv_d != 0 && inv_d != 1) inv_d = 0;

            /* Extract left motor distance (mot_maxon_dataG) */
            char mot_maxon_dataG[5];
            for (int i = 0; i < 4; i++) {
                mot_maxon_dataG[i] = rx_data[(offset + 7 + i) % 27];
            }
            mot_maxon_dataG[4] = '\0';
            int target_mm_G = atoi(mot_maxon_dataG);
            if (target_mm_G < 0) target_mm_G = 0;

            /* Extract left motor direction (inv_g) */
            int inv_g = rx_data[(offset + 6) % 27] - '0';
            if (inv_g != 0 && inv_g != 1) inv_g = 0;

            /* Reset encoders before new movement to avoid cumulative offsets */
            __HAL_TIM_SET_COUNTER(&htim3, 0);
            __HAL_TIM_SET_COUNTER(&htim1, 0);
            origin_left = 0;
            origin_right = 0;
            prev_left = 0;
            prev_right = 0;

            /* Convert target distances (mm) to encoder counts with offset correction */
            float distance_per_count = WHEEL_CIRCUMFERENCE / ENCODER_COUNTS_PER_REV;
            int32_t counts_D = (int32_t)((float)target_mm_D / 1000.0f / distance_per_count) - OFFSET_CORRECTION;
            int32_t counts_G = (int32_t)((float)target_mm_G / 1000.0f / distance_per_count) - OFFSET_CORRECTION;
            target_left = origin_left + (inv_g == 0 ? counts_G : -counts_G);
            target_right = origin_right + (inv_d == 0 ? counts_D : -counts_D);

            /* Log start conditions for debugging */
            printf("Start: left=%d, right=%d, Target: left=%ld, right=%ld\r\n",
                   (int16_t)__HAL_TIM_GET_COUNTER(&htim3), (int16_t)__HAL_TIM_GET_COUNTER(&htim1),
                   target_left, target_right);

            /* Enable position control if not locked */
            if (!control_locked) {
                position_control_active = (target_mm_D > 0 || target_mm_G > 0);
                v_L_base = (target_mm_G > 0) ? low_speed : 0;
                v_R_base = (target_mm_D > 0) ? (int)(low_speed * right_motor_compensation) : 0;
                inv_L = inv_g;
                inv_R = inv_d;
                is_straight = (target_mm_G == target_mm_D) && (inv_L == inv_R);
                if (is_straight) {
                    s = (inv_L == 0) ? 1 : -1;
                } else {
                    e_sum = 0.0f; /* Reset integral error for non-straight motion */
                }
                mot_maxon_both(v_R_base, inv_R, v_L_base, inv_L);
                left_reached_count = 0;
                right_reached_count = 0;
            }

            /* Transmit servo data */
            char servo_goal_data[13];
            servo_goal_data[0] = '<';
            for (int i = 0; i < 12; i++) {
                servo_goal_data[i + 1] = rx_data[(offset + 11 + i) % 27];
            }
            HAL_UART_Transmit(&huart4, (uint8_t *)servo_goal_data, 13, HAL_MAX_DELAY);

            /* Transmit stepper motor 1 data */
            char stepper_data1[2];
            for (int i = 0; i < 2; i++) {
                stepper_data1[i] = rx_data[(offset + 23 + i) % 27];
            }
            HAL_UART_Transmit(&huart3, (uint8_t *)stepper_data1, 2, HAL_MAX_DELAY);

            /* Transmit stepper motor 2 data */
            char stepper_data2[2];
            for (int i = 0; i < 2; i++) {
                stepper_data2[i] = rx_data[(offset + 25 + i) % 27];
            }
            HAL_UART_Transmit(&huart1, (uint8_t *)stepper_data2, 2, HAL_MAX_DELAY);

            /* Reset odometry and encoders if last byte is '1' */
            if (rx_data[(offset + 26) % 27] == '1') {
                x = 0.0f;
                y = 0.0f;
                theta = 0.0f;
                __HAL_TIM_SET_COUNTER(&htim3, 0);
                __HAL_TIM_SET_COUNTER(&htim1, 0);
                prev_left = 0;
                prev_right = 0;
                origin_left = 0;
                origin_right = 0;
                total_dist_left = 0.0f;
                total_dist_right = 0.0f;
                e_sum = 0.0f;
                position_control_active = false;
                control_locked = false;
                mot_maxon_both(0, 0, 0, 0);
                printf("Odometry, encoder counters, and total distances reset to 0\r\n");
            }

            /* Clear UART receive buffer */
            memset(rx_data, 0, sizeof(rx_data));
        }

        /* Restart UART reception */
        HAL_UART_Receive_IT(&hlpuart1, (uint8_t *)rx_data, sizeof(rx_data));

        /* Update odometry and control every 10 ms */
        uint32_t current_time = HAL_GetTick();
        if (current_time - last_update_time >= 10) {
            last_update_time = current_time;

            /* Read current encoder values */
            int16_t curr_left = (int16_t)__HAL_TIM_GET_COUNTER(&htim3);
            int16_t curr_right = (int16_t)__HAL_TIM_GET_COUNTER(&htim1);

            /* Calculate encoder deltas with overflow handling */
            int32_t delta_left = (int32_t)curr_left - (int32_t)prev_left;
            int32_t delta_right = (int32_t)curr_right - (int32_t)prev_right;
            if (delta_left < -32768) delta_left += 65536;
            else if (delta_left > 32768) delta_left -= 65536;
            if (delta_right < -32768) delta_right += 65536;
            else if (delta_right > 32768) delta_right -= 65536;

            /* Update previous encoder values */
            prev_left = curr_left;
            prev_right = curr_right;

            /* Calculate distances traveled */
            float dist_left = (float)delta_left * WHEEL_CIRCUMFERENCE / ENCODER_COUNTS_PER_REV;
            float dist_right = (float)delta_right * WHEEL_CIRCUMFERENCE / ENCODER_COUNTS_PER_REV;

            /* Update total distances */
            total_dist_left += fabs(dist_left);
            total_dist_right += fabs(dist_right);

            /* Position control logic */
            if (position_control_active && !control_locked) {
                /* Check if wheels have reached their targets */
                bool left_reached = (inv_L == 0) ? (curr_left >= target_left - ENCODER_TOLERANCE) :
                                                  (curr_left <= target_left + ENCODER_TOLERANCE);
                bool right_reached = (inv_R == 0) ? (curr_right >= target_right - ENCODER_TOLERANCE) :
                                                   (curr_right <= target_right + ENCODER_TOLERANCE);

                /* Set speeds: stop wheel if target reached */
                int v_L_applied = left_reached ? 0 : v_L_base;
                int v_R_applied = right_reached ? 0 : v_R_base;

                /* Apply PI controller for straight-line motion */
                if (is_straight && !left_reached && !right_reached) {
                    float e = s * (dist_right - dist_left); /* Error: difference in distances */
                    e_sum += e * 0.01f;                     /* Update integral term */
                    if (e_sum > 0.1f) e_sum = 0.1f;        /* Limit integral term */
                    if (e_sum < -0.1f) e_sum = -0.1f;
                    int Delta_v_L = (int)(K_p * e + K_i * e_sum); /* PI adjustment */
                    int Delta_v_R = -Delta_v_L;
                    v_L_applied += Delta_v_L;
                    v_R_applied += Delta_v_R;
                    if (v_L_applied > 1999) v_L_applied = 1999; /* Limit speeds */
                    if (v_L_applied < 0) v_L_applied = 0;
                    if (v_R_applied > 1999) v_R_applied = 1999;
                    if (v_R_applied < 0) v_R_applied = 0;
                }

                /* Log when each wheel reaches its target */
                if (left_reached && left_reached_count == 0) {
                    printf("Left wheel reached: left=%d\r\n", curr_left);
                    left_reached_count = 1;
                }
                if (!left_reached) {
                    left_reached_count = 0;
                }

                if (right_reached && right_reached_count == 0) {
                    printf("Right wheel reached: right=%d\r\n", curr_right);
                    right_reached_count = 1;
                }
                if (!right_reached) {
                    right_reached_count = 0;
                }

                /* Apply adjusted speeds to motors */
                mot_maxon_both(v_R_applied, inv_R, v_L_applied, inv_L);

                /* Debug: print applied speeds every 10 iterations */
                static uint8_t speed_print_counter = 0;
                speed_print_counter++;
                if (speed_print_counter >= 10) {
                    speed_print_counter = 0;
                    printf("Speeds: v_L_applied=%d, v_R_applied=%d\r\n", v_L_applied, v_R_applied);
                }

                /* Stop control when both wheels reach their targets */
                if (left_reached && right_reached) {
                    position_control_active = false;
                    control_locked = true;
                    v_L_base = 0;
                    v_R_base = 0;
                    e_sum = 0.0f;
                    mot_maxon_both(100, !inv_R, 100, !inv_L); /* Brief reverse pulse to stop inertia */
                    HAL_Delay(50); /* Adjust duration if needed */
                    mot_maxon_both(0, 0, 0, 0);
                    printf("Target position reached: left=%d, right=%d\r\n", curr_left, curr_right);
                }
            }

            /* Update odometry */
            float delta_dist = (dist_left + dist_right) / 2.0f;
            float delta_theta = (dist_right - dist_left) / WHEEL_BASE;
            x += delta_dist * cosf(theta);
            y += delta_dist * sinf(theta);
            theta += delta_theta;
            while (theta > M_PI) theta -= 2 * M_PI;
            while (theta < -M_PI) theta += 2 * M_PI;

            /* Send odometry data every 10 iterations */
            static uint8_t odom_send_counter = 0;
            odom_send_counter++;
            if (odom_send_counter >= 10) {
                odom_send_counter = 0;
                char odom_str[64];
                snprintf(odom_str, sizeof(odom_str), "x:%.3f,y:%.3f,theta:%.3f\r\n", x, y, theta);
                HAL_UART_Transmit(&huart5, (uint8_t *)odom_str, strlen(odom_str), HAL_MAX_DELAY);
            }

            /* Debug: print pose and encoder data every 10 iterations */
            static uint8_t print_counter = 0;
            print_counter++;
            if (print_counter >= 10) {
                print_counter = 0;
                printf("Pose: x=%.3f m, y=%.3f m, theta=%.3f rad, left=%d, delta_left=%ld, dist_left=%.3f m, right=%d, delta_right=%ld, dist_right=%.3f m, total_left=%.3f m, total_right=%.3f m\r\n",
                       x, y, theta, curr_left, delta_left, dist_left, curr_right, delta_right, dist_right, total_dist_left, total_dist_right);
            }
        }
    }
}

/**
  * @brief System Clock Configuration
  * @retval None
  */
void SystemClock_Config(void)
{
    RCC_OscInitTypeDef RCC_OscInitStruct = {0};
    RCC_ClkInitTypeDef RCC_ClkInitStruct = {0};

    /* Configure voltage scaling */
    if (HAL_PWREx_ControlVoltageScaling(PWR_REGULATOR_VOLTAGE_SCALE1) != HAL_OK)
    {
        Error_Handler();
    }

    /* Initialize oscillators */
    RCC_OscInitStruct.OscillatorType = RCC_OSCILLATORTYPE_HSI;
    RCC_OscInitStruct.HSIState = RCC_HSI_ON;
    RCC_OscInitStruct.HSICalibrationValue = RCC_HSICALIBRATION_DEFAULT;
    RCC_OscInitStruct.PLL.PLLState = RCC_PLL_ON;
    RCC_OscInitStruct.PLL.PLLSource = RCC_PLLSOURCE_HSI;
    RCC_OscInitStruct.PLL.PLLM = 1;
    RCC_OscInitStruct.PLL.PLLN = 10;
    RCC_OscInitStruct.PLL.PLLP = RCC_PLLP_DIV7;
    RCC_OscInitStruct.PLL.PLLQ = RCC_PLLQ_DIV2;
    RCC_OscInitStruct.PLL.PLLR = RCC_PLLR_DIV2;
    if (HAL_RCC_OscConfig(&RCC_OscInitStruct) != HAL_OK)
    {
        Error_Handler();
    }

    /* Configure clock sources */
    RCC_ClkInitStruct.ClockType = RCC_CLOCKTYPE_HCLK|RCC_CLOCKTYPE_SYSCLK
                                |RCC_CLOCKTYPE_PCLK1|RCC_CLOCKTYPE_PCLK2;
    RCC_ClkInitStruct.SYSCLKSource = RCC_SYSCLKSOURCE_PLLCLK;
    RCC_ClkInitStruct.AHBCLKDivider = RCC_SYSCLK_DIV1;
    RCC_ClkInitStruct.APB1CLKDivider = RCC_HCLK_DIV2;
    RCC_ClkInitStruct.APB2CLKDivider = RCC_HCLK_DIV1;

    if (HAL_RCC_ClockConfig(&RCC_ClkInitStruct, FLASH_LATENCY_4) != HAL_OK)
    {
        Error_Handler();
    }
}

/**
  * @brief LPUART1 Initialization Function
  * @param None
  * @retval None
  */
static void MX_LPUART1_UART_Init(void)
{
    hlpuart1.Instance = LPUART1;
    hlpuart1.Init.BaudRate = 115200;
    hlpuart1.Init.WordLength = UART_WORDLENGTH_8B;
    hlpuart1.Init.StopBits = UART_STOPBITS_1;
    hlpuart1.Init.Parity = UART_PARITY_NONE;
    hlpuart1.Init.Mode = UART_MODE_TX_RX;
    hlpuart1.Init.HwFlowCtl = UART_HWCONTROL_NONE;
    hlpuart1.Init.OneBitSampling = UART_ONE_BIT_SAMPLE_DISABLE;
    hlpuart1.AdvancedInit.AdvFeatureInit = UART_ADVFEATURE_NO_INIT;
    if (HAL_UART_Init(&hlpuart1) != HAL_OK)
    {
        Error_Handler();
    }
}

/**
  * @brief UART4 Initialization Function
  * @param None
  * @retval None
  */
static void MX_UART4_Init(void)
{
    huart4.Instance = UART4;
    huart4.Init.BaudRate = 115200;
    huart4.Init.WordLength = UART_WORDLENGTH_8B;
    huart4.Init.StopBits = UART_STOPBITS_1;
    huart4.Init.Parity = UART_PARITY_NONE;
    huart4.Init.Mode = UART_MODE_TX_RX;
    huart4.Init.HwFlowCtl = UART_HWCONTROL_NONE;
    huart4.Init.OverSampling = UART_OVERSAMPLING_16;
    huart4.Init.OneBitSampling = UART_ONE_BIT_SAMPLE_DISABLE;
    huart4.AdvancedInit.AdvFeatureInit = UART_ADVFEATURE_NO_INIT;
    if (HAL_UART_Init(&huart4) != HAL_OK)
    {
        Error_Handler();
    }
}
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

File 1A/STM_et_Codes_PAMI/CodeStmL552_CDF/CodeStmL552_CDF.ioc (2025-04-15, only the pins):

Mcu.UserName=STM32L552CCTx
PA2.Signal=USART2_TX
PA3.Signal=USART2_RX
PA4.GPIO_Label=X1
PA4.Signal=ADCx_IN9
PA5.GPIO_Label=X2
PA5.Signal=ADCx_IN10
PA6.GPIO_Label=X3
PA6.Signal=ADCx_IN11
PA7.GPIO_Label=X4
PA7.Signal=ADCx_IN12
PA8.GPIO_Label=Servo2
PA8.Signal=S_TIM1_CH1
PA9.GPIO_Label=Servo1
PA9.Signal=S_TIM1_CH2
PB0.GPIO_Label=Button
PB0.Signal=GPXTI0
PB12.GPIO_Label=TRIG
PB12.Signal=GPIO_Output
PB13.GPIO_Label=ECHO
PB13.Signal=GPXTI13
PB5.GPIO_Label=AIN1
PB5.Signal=GPIO_Output
PB6.GPIO_Label=PWMA
PB6.Signal=S_TIM4_CH1
PB7.GPIO_Label=STBY
PB7.Signal=GPIO_Output
PB8.GPIO_Label=BIN2
PB8.Signal=GPIO_Output
PB9.GPIO_Label=PWMB
PB9.Signal=S_TIM4_CH4
PH3-BOOT0.GPIO_Label=BIN1
PH3-BOOT0.Signal=GPIO_Output

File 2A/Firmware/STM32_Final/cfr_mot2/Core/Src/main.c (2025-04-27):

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
/* Includes ------------------------------------------------------------------*/
#include "main.h"

/* USER CODE BEGIN Includes */
#include <string.h>
#include <stdio.h>
#include "servo.h"
#include "maxon.h"
/* USER CODE END Includes */

UART_HandleTypeDef hlpuart1;
UART_HandleTypeDef huart4;
UART_HandleTypeDef huart2;
UART_HandleTypeDef huart3;

TIM_HandleTypeDef htim1;
TIM_HandleTypeDef htim2;

/* USER CODE BEGIN PV */
char rx_data[26];//13 de base
char newline[] = "\r\n";
int i = 0;


/* USER CODE END PV */

void SystemClock_Config(void);
static void MX_GPIO_Init(void);
static void MX_TIM2_Init(void);
static void MX_LPUART1_UART_Init(void);
static void MX_TIM1_Init(void);
static void MX_USART2_UART_Init(void);
static void MX_USART3_UART_Init(void);
static void MX_UART4_Init(void);
/**
  * @brief  The application entry point.
  * @retval int
  */
int main(void)
{

  /* MCU Configuration--------------------------------------------------------*/

  /* Reset of all peripherals, Initializes the Flash interface and the Systick. */
  HAL_Init();

  /* Configure the system clock */
  SystemClock_Config();

  /* Initialize all configured peripherals */
  MX_GPIO_Init();
  MX_TIM2_Init();
  MX_LPUART1_UART_Init();
  MX_TIM1_Init();
  MX_USART2_UART_Init();
  MX_USART3_UART_Init();
  MX_UART4_Init();
  /* USER CODE BEGIN 2 */
  HAL_TIM_PWM_Start(&htim2, TIM_CHANNEL_3); //PB10 TIM2 CH3
  HAL_TIM_PWM_Start(&htim2, TIM_CHANNEL_4); //PB11 TIM2 CH4
  HAL_TIM_PWM_Start(&htim1, TIM_CHANNEL_1); //PA8
  HAL_TIM_PWM_Start(&htim1, TIM_CHANNEL_2); //PA9
  HAL_TIM_PWM_Start(&htim1, TIM_CHANNEL_3); //PA10
  HAL_UART_Receive_IT(&hlpuart1, (uint8_t *)rx_data, sizeof(rx_data));
  /* USER CODE END 2 */

  /* Infinite loop */
  /* USER CODE BEGIN WHILE */
  while (1)
  {

	  // Pour le moteur Maxon droit
	  //char direction_d = rx_data[0]; // Premier caractère pour la direction
	  char mot_maxon_dataD[5];      // 4 caractères + '\0' pour la vitesse
	  strncpy(mot_maxon_dataD, (char *)&rx_data[1], 4);
	  mot_maxon_dataD[4] = '\0';    // Null terminate
	  int mot_maxon_valueD = atoi(mot_maxon_dataD);
	  int inv_d = rx_data[0] - '0';
	  mot_maxonD(mot_maxon_valueD, inv_d);//

	  // Pour le moteur Maxon gauche
	  //char direction_g = rx_data[5]; // Premier caractère pour la direction
	  char mot_maxon_dataG[5];      // 4 caractères + '\0' pour la vitesse
	  strncpy(mot_maxon_dataG, (char *)&rx_data[6], 4);
	  mot_maxon_dataG[4] = '\0';    // Null terminate
	  int mot_maxon_valueG = atoi(mot_maxon_dataG);
	  int inv_g = rx_data[5] - '0';
	  mot_maxonG(mot_maxon_valueG, inv_g);

	  // Pour les servos (12 octets : rx_data[10] à rx_data[21])
	  char servo_goal_data[14];
	  memcpy(servo_goal_data, (char *)&rx_data[10], 12);
	  //servo_goal_data[12] = '\0'; // Optionnel si les données ne sont pas une chaîne
	  servo_goal_data[12] = '\r'; // Ajouter retour chariot
	  servo_goal_data[13] = '\n'; // Ajouter nouvelle ligne
	  HAL_UART_Transmit(&huart4, (uint8_t *)servo_goal_data, strlen(servo_goal_data), HAL_MAX_DELAY);

	  // Steppers (rx_data[22] à rx_data[25]) - Scindé en deux UARTs
	  // Première partie (PCB 1) via huart3 : rx_data[22] et rx_data[23]
	  char stepper_data1[2];
	  memcpy(stepper_data1, (char *)&rx_data[22], 2);
	  HAL_UART_Transmit(&huart3, (uint8_t *)stepper_data1, 2, HAL_MAX_DELAY);

//	  // Deuxième partie (PCB 2) via huart2 : rx_data[24] et rx_data[25], attendre PCB
//	  char stepper_data2[2];
//	  memcpy(stepper_data2, (char *)&rx_data[24], 2);
//	  HAL_UART_Transmit(&huart2, (uint8_t *)stepper_data2, 2, HAL_MAX_DELAY);




	  //servo_goal_data[4] = '\r'; // Ajouter retour chariot
	  //servo_goal_data[5] = '\n';
	  //HAL_UART_Transmit(&huart3, (uint8_t *)servo_goal_data, 5, HAL_MAX_DELAY);

//	  // Transmission pour debug
//	  char message[28]; // 26 caractères de rx_data + 2 pour "\r\n"
//	  memcpy(message, rx_data, 26); // Copier rx_data dans message
//	  message[26] = '\r'; // Ajouter retour chariot
//	  message[27] = '\n'; // Ajouter nouvelle ligne
//	  HAL_UART_Transmit(&huart2, (uint8_t *)message, sizeof(message), HAL_MAX_DELAY);



    /* USER CODE END WHILE */

    /* USER CODE BEGIN 3 */
  }
  /* USER CODE END 3 */
}

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
/* USER CODE BEGIN 4 */
void HAL_UART_RxCpltCallback(UART_HandleTypeDef *huart)
{
	if (huart == &hlpuart1) {
		// Réactiver la réception immédiatement
		HAL_UART_Receive_IT(&hlpuart1, (uint8_t *)rx_data, sizeof(rx_data));
	}
}
/* USER CODE END 4 */
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


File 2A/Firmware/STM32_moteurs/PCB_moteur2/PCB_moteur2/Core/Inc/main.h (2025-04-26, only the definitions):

#define MOTOR_EN_Pin GPIO_PIN_13
#define MOTOR_EN_GPIO_Port GPIOC
#define ENC_A_Pin GPIO_PIN_0
#define ENC_A_GPIO_Port GPIOC
#define ENC_B_Pin GPIO_PIN_1
#define ENC_B_GPIO_Port GPIOC
#define ENC_Z_Pin GPIO_PIN_2
#define ENC_Z_GPIO_Port GPIOC
#define USR_BTN_2_Pin GPIO_PIN_4
#define USR_BTN_2_GPIO_Port GPIOA
#define CMD_TX_Pin GPIO_PIN_4
#define CMD_TX_GPIO_Port GPIOC
#define CMD_RX_Pin GPIO_PIN_5
#define CMD_RX_GPIO_Port GPIOC
#define VCP_TX_Pin GPIO_PIN_10
#define VCP_TX_GPIO_Port GPIOB
#define VCP_RX_Pin GPIO_PIN_11
#define VCP_RX_GPIO_Port GPIOB
#define BUS_V_Pin GPIO_PIN_12
#define BUS_V_GPIO_Port GPIOB
#define BUS_Imes_Pin GPIO_PIN_14
#define BUS_Imes_GPIO_Port GPIOB
#define USR_LED_4_Pin GPIO_PIN_15
#define USR_LED_4_GPIO_Port GPIOA
#define USR_LED_3_Pin GPIO_PIN_10
#define USR_LED_3_GPIO_Port GPIOC
#define USR_LED_2_Pin GPIO_PIN_11
#define USR_LED_2_GPIO_Port GPIOC
#define USR_LED_1_Pin GPIO_PIN_12
#define USR_LED_1_GPIO_Port GPIOC
#define USR_BTN_1_Pin GPIO_PIN_2
#define USR_BTN_1_GPIO_Port GPIOD
#define USR_BTN_3_Pin GPIO_PIN_6
#define USR_BTN_3_GPIO_Port GPIOB

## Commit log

2024-07-09 Update Summer_Tasks.md
    Ajout de premiers descriptifs du PCB
2024-07-10 Update Summer_Tasks.md
    correction fautes de frappe et précisions supplémentaires:
    - JETSON
    - Images ou LiDAR
    - ordi et 4 caméras
2024-08-19 ROS PORTUGAL
    je vous invite à lire les diapos si vous avez un peu de temps pour être plus frais au sujet de ros.
2024-09-17 summer work on the MB
    [Alim.kicad_sch, Rpi.kicad_sch, buck5V.kicad_sch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]
2024-09-17 réarranger dossiers
    [Alim.kicad_sch, Rpi.kicad_sch, buck5V.kicad_sch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]
2024-09-17 adding to hardware
    [ALIMENTATION.kicad_sch, Connecteurs.kicad_sch, GPIO_3V3_Connector.kicad_sch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]
2024-09-24 Rename Capture d’écran du 2024-09-24 14-06-27.png to Roue_BaneBots_30A.png
2024-09-24 Rename Capture d’écran du 2024-09-24 13-59-06.png to T81_Hub_BaneBots
2024-09-24 Rename Capture d’écran du 2024-09-24 14-07-55.png to Roues_BaneBOts_40A
2024-09-28 Ajout de cours de ROS provenant de l'ESIEE Paris
    [complex_robot.yaml, simple_robot.yaml]
2024-10-01 Adding motor board
    [20230830_1341_Inverter_KiCAD.csv, Alim.kicad_sch, Arm_IRF540NBbF.kicad_sch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]
2024-10-08 update schematic
    [Arm_IRF540NBbF.kicad_sch, FAN.kicad_sch, Inverter_KiCAD.kicad_sch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]
2024-10-12 last schematic editing
    just miss a FB resistor value
    [Inverter_KiCAD.kicad_sch, MCU_STM32G474.kicad_sch]
2024-10-13 project stm32 for simple uart connexion with pi
2024-10-18 deut routage
    [20230830_1341_Inverter_KiCAD.csv, ALIMENTATION.kicad_sch, Alim.kicad_sch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]
2024-10-20 almost finished pcb
    [Inverter_KiCAD.kicad_pcb, Inverter_KiCAD.kicad_sch, MCU_STM32G474.kicad_sch]
2024-10-21 finalization
    Rooting and last edits ready to go
    [Inverter_KiCAD.kicad_pcb, Inverter_KiCAD.kicad_sch, MCU_STM32G474.kicad_sch]
2024-10-21 PCB motor oof
    [Inverter_KiCAD.kicad_pcb, Inverter_KiCAD.kicad_sch, MCU_STM32G474.kicad_sch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]
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2024-10-22 Done !
    [Inverter_KiCAD.kicad_pcb]
2024-10-24 cfr_moteurs qui fonctionne avec l'uart et la stm32
2024-11-12 approaching end of schematics
    [buck5V.kicad_sch, buck7.4V.kicad_sch, stm32.kicad_sch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]
2024-11-13 quite finished schematics
    [stm32.kicad_sch, test1.kicad_sch]
2024-11-14 finished schematics missing footprints
    [buck5V.kicad_sch, stm32.kicad_sch, test1.kicad_pcb]
2024-11-17 beginning of PCB design with Rpi4 shield shape
    [stm32.kicad_sch, test1.kicad_pcb, test1.kicad_sch]
2024-11-18 Motherboard advance
    [stm32.kicad_sch, test1.kicad_pcb]
2024-11-19 MotherBoard finished
    [stm32.kicad_sch, test1.kicad_pcb, test1.kicad_sch]
2024-11-19 Mainboard Done !
    [stm32.kicad_sch, test1.kicad_pcb]
2024-11-19 Stepper Board schematic begin
    [Stepper.kicad_pcb, Stepper.kicad_sch]
2024-11-20 Updating t
    [stm32.kicad_sch, test1.kicad_pcb, test1.kicad_sch]
2024-11-20 Edits of the PCB done
    [test1.kicad_pcb]
2024-11-21 added 1A and 2A directories
    [20230830_1341_Inverter_KiCAD.csv, ALIMENTATION.kicad_sch, Alim.kicad_sch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]
2024-11-21 Ajout du projet Kicad PAMI 2425
    [PCB_PAMI_STMF3.kicad_pcb, PCB_PAMI_STMF3.kicad_sch]
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2024-12-10 Commit ros2 pour pkg lidar. Merci au manager d'Ares, petit prince de Bretagne, soleil de l'ENSEA, empereur autoproclamé d'Ares, le British Napoleon pour sa décisivité dans ce commit et son assertivit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
2024-12-10 evolution of the stepper board
    [Stepper.kicad_pcb, Stepper.kicad_sch, Stepper.step]
2024-12-17 add recovery for router1
    [MultipriseXT60.kicad_pcb, MultipriseXT60.kicad_sch, Stepper.kicad_pcb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]
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2025-01-24 Mainboard v2
    [Alim.kicad_sch, BOM_MainBoard.csv, Rpi.kicad_sch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]
2025-01-24 Readme initialement sur un fork, reamenagement des fichiers
2025-01-28 Centralisation du projet sur le workspace ros2_ws et intégration de la node qui permet aux moteurs de s'arrêter au signal du Lidar
2025-01-28 Correction PCB Servo LF
    [PCB_Servo.kicad_pcb, PCB_Servo.kicad_sch]
2025-01-28 Check Multiprise LF La grille PTN!
    [MultipriseXT60.kicad_pcb]
2025-01-28 last minute update
    [test1-B_Cu.gbr, test1-B_Mask.gbr, test1-B_Paste.gbr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]
2025-01-28 recommit to be sure...
    [Stepper.kicad_pcb, Stepper.kicad_sch]
2025-01-29 change on kicad projects, remove errors
    [MultipriseXT60.kicad_pcb, MultipriseXT60.kicad_sch, Stepper.kicad_pcb]
2025-01-30 Ajout launch lidar+serial avec arrêt, autrement dit robot homologable
2025-02-04 ajout du répertoire PCB_PAMI contenant la version finale du PCB
    [Janus_finalV.kicad_pcb, Janus_finalV.kicad_sch, PCB_PAMI_STMF3.kicad_pcb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]
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2025-02-10 Projet STM32 pour communication à 11 caractères (fonctionne avec la node robot_controle_node_3.py
2025-02-10 Mainboard v3
    [stm32.kicad_sch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]
2025-02-12 PCB v3
    [stm32.kicad_sch, test1.kicad_pcb]
2025-02-12 didn't save lol
    [stm32.kicad_sch]
2025-02-12 last details
    [test1.kicad_pcb]
2025-02-13 ajout de l'écran stm32 pour display les différents bags disponibles (dans le package serial node). Merci à Antoine Lemarignier pour son assertivité
2025-03-04 écran_stm
    [20230830_1341_Inverter_KiCAD.csv, Alim.kicad_sch, Arm_IRF540NBbF.kicad_sch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]
2025-03-04 correction en théorie
    [20230830_1341_Inverter_KiCAD.csv, Alim.kicad_sch, Arm_IRF540NBbF.kicad_sch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]
2025-03-18 stm32 code for fixing kenny's mistakes pcb output pwm
    [PCB_moteur2.ioc, main.c, main.h]
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2025-04-01 pcb edits
    [Inverter_KiCAD-B_Cu.gbr, Inverter_KiCAD-B_Mask.gbr, Inverter_KiCAD-B_Paste.gbr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]
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2025-04-27 Update README.md
    fixation pcb, antennes et routeur
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2025-04-28 last main board edis
    [Alim.kicad_sch, BOM_MainBoard.csv, Rpi.kicad_sch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]
2025-04-28 Last pcb edits for the motor board
    [20230830_1341_Inverter_KiCAD.csv, Arm_IRF540NBbF.kicad_sch, FAN.kicad_sch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]
2025-05-24 bag_playback (fusion du lanceur de bag et du bag listener avec démarrage écran tirette )

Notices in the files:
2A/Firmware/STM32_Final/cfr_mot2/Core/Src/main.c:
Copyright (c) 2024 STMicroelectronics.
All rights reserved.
